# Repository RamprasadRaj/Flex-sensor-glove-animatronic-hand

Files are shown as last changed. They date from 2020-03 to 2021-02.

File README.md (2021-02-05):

# Flex sensor glove animatronic hand
Repository containing the information and files for flex sensor glove controlled 3 DoF animatronic hand
## Demo
This project deals with design, fabrication, and control of 3 finger 3 DoF animatronic hand mimicking flex sensor glove worn by human operator

[](https://youtu.be/1zQ_faMaoO8)

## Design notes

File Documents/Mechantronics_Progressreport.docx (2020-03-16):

MEGN540 - Project Progress Report

Ramprasad Rajagopalan

Bhuvan Tej Kanigiri

Technical:

What problem are you solving?

The project aims to design, fabricate and control 3 finger animatronic hand mirroring fingers movements made by a human operator. The project addresses a method to capture motion of fingers using flex sensors and fabricating a custom PCB to process, power and control the animatronic hand.

What is your design concept?

The hand design consists of three fingers viz., thumb, index and middle finger, with 1 DOF. Each finger has three portions viz., proximal, medial and distal portions. The different portions of the fingers are joint together with 1 or 2 springs and hinges on the dorsal side of the hand. 3D printing technique is utilised for printing each portion of the hand. Each finger is driven by a fishing line placed eccentrically on the palmer side of the hand. The finger movements are driven by the servo motors. One end of the fishing line is tied to the distal end of the finger and the other end is tied to the horn of the servo motor. The routing of the fishing line inside each finger is facilitated by having plastic straws enclosed within a hollow section. The entire setup is mounted on a platform having the custom PCB and power supply.

The glove design has flex sensors stitched to each finger for the entire length. The flex sensors are connected directly to the custom PCB by extending the wires. Later design may include wireless implementation.

What Sensors and Actuators will you use?

Here we are using flex sensors (datasheet (https://www.sparkfun.com/datasheets/Sensors/Flex/flex22.pdf)), which captures the bending movement data.

We are using an MG995 servo (datasheet (https://www.electronicoscaldas.com/datasheet/MG995_Tower-Pro.pdf)), which drives the animatronics hand.

What will your PCB do?

The custom PCB has the following components delivering certain processes.

- ATMega328P sits on a PCB board for all the required processing and communication purposes like converting flex sensor’s output voltage (digital output - ADC) to PWM timings (range: 0.388 - 2.14ms), in turn it calculates the duty cycle for the servo motor for the desired rotations, which finally replicates the human finger’s position.
- Potentiometer placed in the -ve terminal of the flex sensor would help in adjusting the sensitivity for the input users hand movement.
- Voltage regulator circuit to power the servo motors, sensors and ATMega328 separately.
- ICSP header to connect the external programmer to flash.
- Power jack to connect the external power supply.

All the heavy lifting is done in PCB and finally it sends the PWM commands to the servo motors.

What is your high-level integration plan?

Step 1: Human hand (uses a glove, where 3 flex sensors are attached to the 3 finger) gives finger movements, which are encoded in terms of resistance. Change of resistance in the three fingers implicitly knows how much it is moved - this is done using flex sensors. Take the analog output from the flex sensor, give it to ADC for conversion.

(https://www.google.com/aclk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)Step 2: Atmega328P receives this signal and converts that into a PWM signal using TIMERS.

Step 3: Finally power and PWM signal are sent to the servo motor on the animatronics hand.

Programmatic:

What is your project schedule and key milestones?

March 1st - 3rd week: Purchasing materials. 3D printing fingers and handbase. Building a breadboard prototype of the circuit. Pseudo code for reading the flex sensors data. Key milestone would be to have working finger movements in hand and programmable breadboard circuit.

March Fourth week(spring break): Fabricating the glove and writing the embedded C code for calibrating the flex sensor and controlling servo motor position. Implementing a filter to get a smooth response from the sensor. Key milestone would be to calibrate the flex sensor and implement the filter.

April 1st - 2nd week: Design and order the PCB. Testing for repeatability of finger actuation. Completing the left out work. Key milestone would be to have a functioning breadboard prototype of the animatronic hand.

April 3rd week: Further testing with custom PCB and Demo. Key milestone would be to have the PCB functioning with other components.

How have you split up the work?

Mechanical aspects of project: Ramprasad

Electronics aspects of project: Bhuvan Tej

Software aspects of project: both

What are your critical paths?

Arrival of sensors, motors and other components.

Getting the correct mapping of PWM values in the desired ranges.

Scaling is also critical - from the resistors value to the PWM signals.

Correct PCB design without shorting any components and arrival of functional PCB.

What is your current budget estimate?

Our current budget is around 100-120 USD ( ± 20 USD)

What is your highest technical risk and how are you mitigating that risk?

Hardware standpoint:

- As there all lots of electronics included on the PCB, make sure there is no shorting wire on PCB connections before giving supply: Using multimeter check all the connections properly for every iteration of testing it- if possible test in simulation software by giving some random test data within the specific range.
- The motor rotation should not exceed the finger movement limits: Start off with some small scaling component (High resistance for the resistor in series with sensor), then gradually increase it to the desired range.
- There is a chance of abduction/adduction finger movement happening instead of purely flexion/extension movement due to clearance in the joints or uneven force distribution along the finger. Having stoppers or adding 2 springs to each joint of the finger on the dorsal side makes sure that it's not moving sideways.

Software Standpoint:

- There is a chance sampling of some delay occurring from the user's hand movement to the animatronics hand, which can cause some loss of information in turn making the animatronics hand wobble randomly. Having a robust filter and sampling prevents the loss of information.

What is your highest programmatic risk and how are you mitigating that risk?

Higher chance of problem might be only from the hardware design standout point of view, design might change during the testing phase.

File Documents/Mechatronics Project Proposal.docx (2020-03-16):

Project Name: Animatronic Robotic Hand (Bhuvan Tej Kanigiri, Ramprasad Rajagopalan)

Concept proposal: From teleoperation to prosthetic hand development, animatronic hand serves as a “simple” implementation to mimic human hand movements. This project deals with design, fabrication and control of 3 finger 3 DOF animatronic “hand” mimicking flex sensor glove worn by human operator. The user wears the glove and the amount of bending in thumb, index and middle finger will be captured by the flex sensor attached on each finger. The amount of bending or resistance will be wirelessly transferred using custom build PCB to Arduino either over Wifi/bluetooth. The animatronic hand has fingers driven by strings and rubber band. The strings are attached to the servo motor. Based on the amount of bending, the Arduino will generate corresponding movement in the finger by driving the servo motors.

System requirements:

Servo Motors, Flex sensors (2.2”-4”), Arduino, 9v batteries, resistors, connecting pins, glove, thread, rubber band, foam board or cardboard, handbase, spacers and hobby knife.

Total Budget: USD $95 - (Electronic parts - $70, mechanical parts - $25)

Initial project plan:

February | - CAD design of 3 DOF 3 finger animatronics hand and base - Ordering sensor, motors and microcontroller - Working of Flex sensor, servo motors and setting wireless communication using breadboard circuit - Pseudo code and preliminary code for testing - Prototype 1 of hand and glove
March | - Refine CAD model - Design PCB and order - Embedded C code and testing - Prototype 2 of hand

April - Final testing and presentation

Design incorporation:

Interaction with the real world (minimum: one sensor & one affecter) - Flex sensor is attached to each finger on the glove worn by human operator. Servo motor is present to pull corresponding fingers. Embedded programming is used to program the Atmega328 microcontroller to read data from flex sensors and input PWM signals to control servo motor position. PCB design is done for incorporating power and wireless transmission from the glove. Final prototype should be able to mimic finger movement and demonstrate wireless transmission between glove and Arduino.

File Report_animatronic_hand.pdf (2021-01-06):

## Shadow hand - a 3 DoF animatronic hand

Ramprasad Rajagopalan
MS in Mechanical Engineering

rrajagopalan1@mines.edu

Bhuvan Tej Kanigiri
MS in Mechanical Engineering

bhuvantejkanigiri@mines.edu

Abstract

From teleoperation to prosthetic hand development, animatronic hand serves as a “simple” implementation to mimic human hand movements. This project deals with design, fabrication and control of 3 finger 3 DOF animatronic “hand” mimicking flex sensor glove worn by human operator. The user wears the glove and the amount of bending in thumb, index and middle finger is captured by the flex sensor attached on each finger. The amount of bending or resistance is sent to Arduino UNO for processing motor commands. The animatronic hand has fingers driven by strings and rubber band. Based on the amount of bending, the Arduino generates corresponding movement in the finger by driving the servo motors attached with the strings.

### 1. Introduction

### 1.1. Problem statement

Animatronic hand consists of two systems viz., mechatronic system of the hand and glove worn by the human operator. Only 3 degree of freedom(DoF) is considered out of the 27 DoF present in the human hand. These 3 DoF corresponds to flexion and extension of the middle, index and thumb fingers. The design problem is illustrated in Fig.1. The glove system consists of a design to capture the flexion and extension of each fingers. This can be done by using flex sensors or strain gauges attached to each finger. The flex sensors are placed on the dorsal side of the hand for easier design implementation. The bending data is sent directly to the micro-controller for processing motor commands. The mechatronic system consists of linkages making up the hand driven directly by the motors or by strings pulled by the motors. The linkages should be proportional to the human anatomical structure. The finger linkages are driven by fishing wire tied to each motor. The design should be done in a way to translate effective motion of the motors to maximum flexion movement of each fingers. The micro-controller should apply motor command values by mapping the input flex sensor data to corresponding angle. The re-

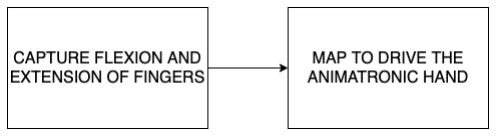
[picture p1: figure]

Figure 1. Design problem representation

quired components for building a 3 DoF animatronic hand driven by flex sensor glove is illustrated in the section below.

### 1.2. System Requirements

Electronics Components

Device name | Model no. | Quantity
Micro Servo Motors | A900 | 3
Flex sensors(2.2” - 4”) | - | 3
Arduino | UNO | 1
Programmer | AVRISP | 1
Resistors | 10K, 220 | 3,3
Jumper cables

Mechanical Components

Device name | Quantity
3D printed hand with hand base | 1
Glove | 1
Fishing thread and rubber band | 1
Insulation tape | 1

Software: Embedded C with Atmel Studio 6 and MAT-LAB for data visualization.

### 2. Approach

### 2.1. Design Implementation

The thumb, index and middle fingers of the right hand are chosen for mimicking the flexion and extension action. These three fingers are commonly used in robotic grippers for object manipulation and pick and place applications. Glove Design: The implemented glove design is shown in the left labelled image of Fig.3. The flex sensor is at-

Finger | Dimensions (mm)
Index Middle Thumb | 21 24 34 | 27 34 - | 48 56 28

Proximal
phalanx

Middle
phalanx

Distal
phalanx

Table 1. Dimension of each fingers

tached along the length on the dorsal side of the glove at roughly in the middle of the finger with tape. Other effective ways of fixing the flex sensor would be beneficial for better response and prevents unforced error in calibration. Animatronic hand design: The assembled CAD model and labelled 3D printed hand are shown in Fig.2 and 3 respectively. The 3D models are designed using Autodesk FUSION 360 software. The hand is designed according to human proportions and measurements as shown in Table.1. The bones in each finger is called as phalanx or phalange. The one closer to the metacarpals or torso of the hand is called as proximal phalanx and the one far from it is called as distal phalanx. The thumb finger is divided into 2 parts

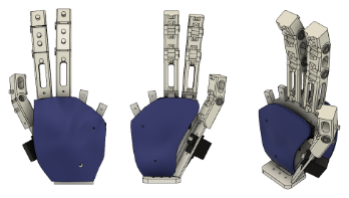
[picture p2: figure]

Figure 2. CAD assembly of animatronic hand

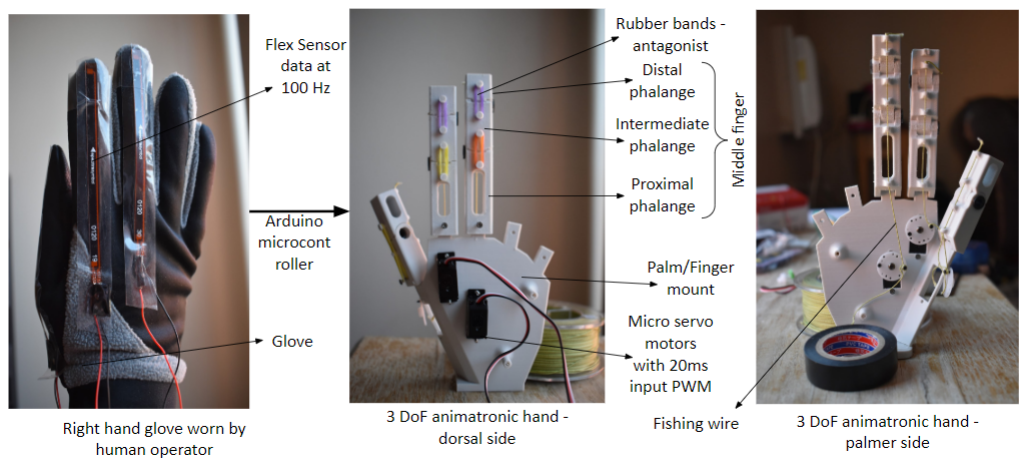
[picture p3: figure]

Figure 3. Labelled overview of solution

viz., proximal and distal phalanges while middle and index fingers are divided into 3 parts viz., proximal, intermediate and distal phalanges. The phalanges revolve relative to one another by revolute joint held with the help of plastic bush bearings. All the fingers are designed with the provision to route the fishing wire on the palmer side by providing extruding portions at end of each phalanx. The finger phalanges are also designed with extrusions at each ends on the dorsal side in order to tie the rubber band to the adjacent phalanges. The palm of the hand is designed in such a way that the thumb finger is fixed out-of-plane, to other fingers, in an opposing position as shown in Fig.2. The palm also has provision at the bottom to fix it onto the table.
One end of the fishing wire is tied to tip of the distal phalanx and other end is tied to the servo motor. The placement of the motors is pivotal in defining the range of motion and force exerted on the finger. The spindle of the servo is attached with round hub for compact design and larger force output. The mounting holes for servo motors are provided appropriately in order for it to be inserted in such a way that the spindle faces the palmer side of the hand. The hand design also consist of two form covers for aesthetic appeal and shielding the internal connections.

### 2.2. PCB Electronics

### 2.2.1 Circuit schematics

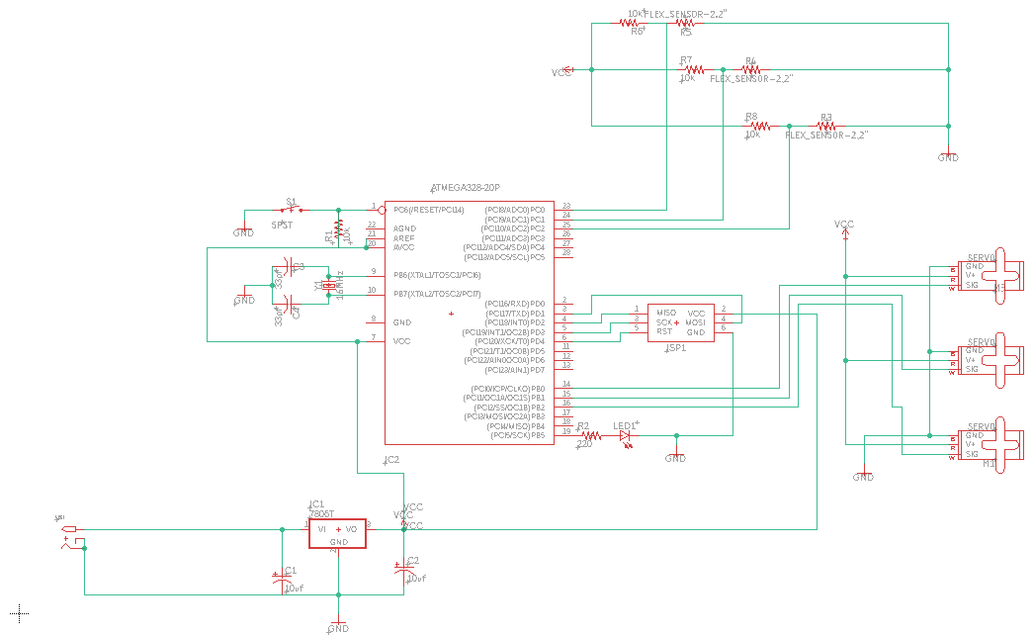
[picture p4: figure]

Figure 4. PCB schematics

Power Module: 12 V adaptor is connected to 7806T voltage regulator which serves to output constant voltage to the MCU section. This supply is given to three servos. MCU Module & Data transfer Module: Used Atmel Studio and AVR ISP programmer to compile the code in the PC and flash the program in the ATMega328P micro-controller.
Pin connections: From ISP to Atmega328P, it has six pins connected to MCU.
Electronics Components
C1: Table.2 is the connection from AVR-ISP programmer to Atmega328P micro controller.
C2: Table.3 is the connection from ATMega328P to flex sensors.
Note: Tapping is done in between the 10k resistor and Flex sensors, both sides are connected to ground and 5V

ISP pin | MCU
MOSI | PD1(TXD)- Pin 3
SPI | PD2(INT0)- Pin 4
Sck | PD3(INT1)- Pin 5
Reset | PD4(XCK/T0) - Pin 6
Vcc | Vin(Any 5v source)
Gnd | Gnd

Table 2. PIN connection between ISP and ATMega328P

MCU | Flex-sensor
PC0(ADC0) | Tapped in b/w Flex-I and 10k resistor(r6)
PC1(ADC1) | Tapped in b/w Flex-II and 10k resistor(r7)
PC2(ADC2) | Tapped in b/w Flex-III and 10k resistor(r8)

Table 3. PIN connections between flex sensor and ATMega328P

MCU | Micro servo motors
PB0 | Signal pin (named W) to servo1
PB1 | Signal pin (named W) to servo2
PB2 | Signal pin (named W) to servo3

Table 4. PIN connections between micro servo motor and AT-Mega328P

MCU | 16MHz Crystal oscillator
PB6(XTAL1) | crystal-oscillator one side
PB7(XTAL2) | crystal-oscillator other side

Table 5. PIN connection between crystal oscillator and AT-Mega328P

supply.
C3: Table.4 is the connection between ATMega328P and Micro-servo motors.
Note: The other two pins in each servo motor is connected to the supply. A 5V supply is provided but for an ideal working of servo motor, 6V is required. Due to lack of step-down converter equipment, suply is provided at 5V. As of now, there won’t be a considerable bias in servo motor characteristics, this is due to the proper threshold mapping done from the flex to servo accordingly by reducing the window.
C4: Table.5 is the connection between ATMega328P and 16MHz crystal oscillator.
I/O Device Module: Flex-sensor is used take input from the environment, where the user bends his hand (change of resistance: which will be the input signal for the EN pin in micro servo motor) and micro-servos act as a output device which bends the animatronics hand.

### 2.3. Programming

### 2.3.1 Motor control

The servo motors can be controlled using PWM signals of 20ms time period in order to make it rotate to the desired angle. The 16-bit TIMER1 of ATMega328P is utilised for generating the PWM signals with desired time period. Multiple PWM outputs can’t be achieved using TIMER1 OC1A pin. Therefore, the output voltage value of PORTB pins are controlled by TIMER1 to drive the servo motors. This can be achieved by comparing the TIMER1 count, TCNT1, value with the required motor voltage, motor vol, to clear the pin and compare match ISR to set the corresponding pin every 20ms. The value of motor vol is obtained from calibration. The clearing and setting of the pin generates the required PWM to control the motor.

### 2.3.2 Calibration

Flex sensor: The flex sensor data is read every 10ms and stored in a buffer. The data is initially streamed to MAT-LAB at 100Hz to record and visualize the signals. The streamed data is free from noise and thus eliminates the need for implementing a filter. The extremities of the data for each finger of a specific human operator are determined for flexion and extension. The values are then recorded for saturation and linear interpolation.
Servo motor: The servo motors has a limited range of motion i.e. from 0 deg to approx. 165 deg. The deadband of the servo motor is identified by setting different values to the motor vol in order to generate different duty cycle. These extremities are also recorded and used in linear interpolation and saturation. After identifying the deadband of servo motor, the round hub is appropriately placed at 0 deg with little tension in the fishing wire. This ensures that the motor pulls the finger right from the start of rotation.

### 2.3.3 Program flow chart

The extremities obtained from the calibration of the sensor and motor are included in the Embedded C program. The sequence of steps followed in programming the Embedded C program is shown in Fig.5. The initialization of the pin is done by setting PORTB pins as output. The TIMER1 is set in Fast-PWM mode with ICR1 as TOP and 8 as the prescalar value. The ICR1 value is chosen as 4999 in a way to generate PWM signals with 20ms time period. ISR for TIMER1 is called every 20ms to set PORTB pin value as HIGH in order to generate a non-inverting PWM signal. The TIMER0 is set in CTC mode with OCR0A as TOP. The value of OCR0A is set in a way to call an ISR on compare match every 10ms to raise flag 0 every 10ms, where flag 0 is defined as a volatile variable. The ADC is initialized with 1024 as prescalar without initialization the

ADMUX channel. By default, the MUX pins are set to read from pin A0.
A while loop is made to run infinitely by iterating through two different conditions. The first condition checks if the TCNT1 value is greater than the duty cycle value and PORTB pin value NOT set. If the condition gets passed then the PORTB pin value is set as LOW or cleared. The value of PORTB pin is set again when ISR of TIMER1 is called every 20ms. In order to reduce the load on the micro-controller to check this statement all time, an entry IF condition can be placed to check if the TCNT1 value lies within certain threshold of the ICR1 value. This helps in improving the performance of the micro-controller.
The second condition gets passed roughly every 10ms when flag 0 is raised. The current ADC value is read and stored. As it is not possible to read simultaneously from 3 analog pins, a SWITCH conditional clause is placed to map the analog value to corresponding motor voltage as well as switch the MUX pins. The ADC value is saturated within the calibration range before mapping. The MUX pin is set to read sequenctially between analog pins A0, A1, A2 and back again to A0. After the MUX pin value is set, another ADC conversion is started. The motor vol determines the duty cycle of the PWM signals.

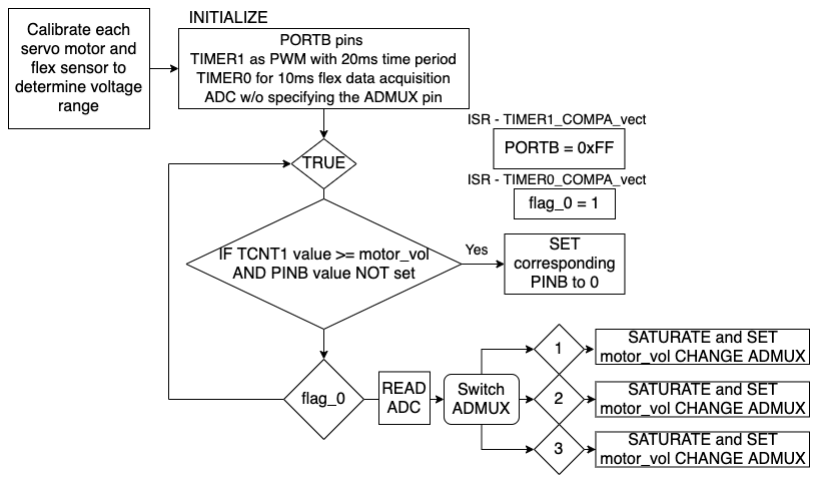
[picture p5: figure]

Figure 5. Pseudo code chart

### 3. Design challenges

The design process has certain critical and challenging steps that needs to be taken into consideration. The animatronic hand should be proportional to human anatomical structure. Unlike the human hand, animatronic hand is not driven by numerous independent linear actuating muscles but driven by single rotating motor. The effective force exerted by the motor depends immensely on the placement height and orientation. Effective pull length of approx. 28mm is delivered by the limited motion of the servo motor. The stiffness of the antagonist rubber band is critical and varies from joint to joint. The effective pull length and stiffness of the rubber band influences the bending angle of each finger. Fig.6 illustrates a finger joint in the actuated condition. The force exerted by the motor acts along the fishing wire. For a given pull length of the wire, the distance from the center of joint to the wire dictates the bending angle of each finger. If the distance increases the bending angle decreases and vice-versa. The effective torque from the motor should overcome the opposing torque of the rubber band. In addition, the opposing torque exerted by the rubber band should be sufficient enough to cause extension of the fingers.

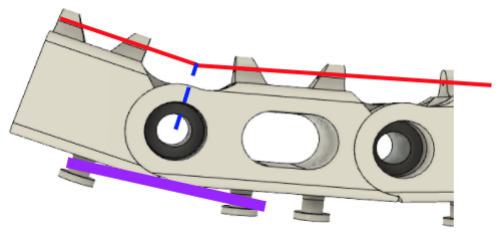
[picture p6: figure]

Figure 6. Side view of finger: Red line - fishing wire, Blue dashed line - distance from joint center and fishing wire and purple line -stretched rubber band

The servo motors with nylon gearing is sensitive to external loads. The gears and potentiometer can be easily damaged if the motor is manually turned. The flex sensor calibration can vary from person to person. Friction in the joints is undesirable and unavoidable in 3D printed parts. By overcoming the above mentioned challenges and considerations, a better design of the animatronic hand can be obtained.

### 4. Future Work and Lessons learnt

The 3 DoF animatronic hand is successfully controlled by tethered flex sensor glove. The next steps is to implement wireless data transfer in order to provide unconstrained interaction to the human operator. This promotes the scope for teleoperation applications. Better motors translate to better performance of the animatronic hand. Custom PCB with power distribution should be ordered and tested.
This project demonstrates the implementation of embedded programming and working with circular buffers. Some of the design challenges can be approached in a more systematic way. Kinematic study should be performed to optimize the geometry. An interactive approach to calibrate the sensor automatically before each run would be beneficial when used for multiple human operators.

### 5. References

[1] CoffeeCup Software, Inc. “The Animatronic Robotic Hand.” Animatronic Robotic Hand, URL. (https://mech.vub.ac.be/teaching/info/mechatronica/finished_projects_2013/team_5/index.html)
[2]“Learn the Fundamentals of Mechatronics!” Micro-controller - Program Transfer Part 1- A Beginners Guide to the Atmel AVR Atmega32, URL. (https://www.newbiehack.com/MicrocontrollerProgramTransferPart1ABeginnersGuidetotheAtmelAVRAtmega32.aspx)

### 6. Appendix

Video Demonstration link: Click here. (https://youtu.be/PWxeIW6LgmQ) Eagle CAD: attached
Embedded Code: attached

# PSEUDO CODE

## Demonstrating embedded programming for reading multiple flex sensor data and controlling multiple servo motors

## PROGRAM: Reading analog values from flex sensors and controlling the servo motors

DESCRIPTION: Flexion and extension of a finger is captured by change in voltage across the flex sensors. The analog voltage is read and mapped to corresponding control voltage for each servo motors. The PWM signal is controlled with TIMER1 at 50Hz and data acquisition is done with TIMER0 at 100Hz.

## FUNCTION: pin_init INPUT: None RETURNS: None

## INITIALIZE data direction register of PORTB, DDRB as OUTPUT

## FUNCTION: timer_init INPUT: None RETURNS: None

## INITIALIZE TCNT1 and TCNT0 as 0, SET TIMER1 in fastPWM mode with ICR1 as 4999 as TOP and

8 as prescaler value to generate non-inverting PWM signals at 50Hz, SET TIMER0 in CTC mode with OCR0A as 156 as TOP and 1024 as prescaler value to raise flag every 10ms and enable interrupts for both timers.

## FUNCTION: ISR INPUT: TIMER1_COMPA_vect RETURNS: None

## SET PORTB as 0xFF (HIGH)

## FUNCTION: ISR INPUT: TIMER0_COMPA_vect RETURNS: None

## flag_0 as 1

## FUNCTION: adc_init INPUT: None RETURNS: None

## INITIALIZE ADMUX and SET REFS0, ENABLE ADC in ADCSRA register with 128 as prescaler value using ADPSx pins

## FUNCTION: adc_read INPUT: None RETURNS: ADC

## RETURN ADC

## FUNCTION: uart_init INPUT: None RETURNS: None

INITIALIZE the baudrate registers UBRR0 and transmission and receiver pins in UCSR0B and SET

## the data bits to be 8-bit long in UCSR0C register

## FUNCTION: uart_transmit INPUT: data RETURNS: None

## UDR0 as data

## FUNCTION: sensor_middle_to_motor INPUT: sense_pos RETURNS: motor_vol

## CALCULATE mapping using linear interpolation to convert sense_pos to motor_vol

## FUNCTION: sensor_index_to_motor INPUT: sense_pos RETURNS: motor_vol

## CALCULATE mapping using linear interpolation to convert sense_pos to motor_vol

## FUNCTION: sensor_thumb_to_motor INPUT: sense_pos RETURNS: motor_vol

## CALCULATE mapping using linear interpolation to convert sense_pos to motor_vol

## FUNCTION: main INPUT: None RETURNS: None

INITIALIZE flexthumb, flexmiddle, flexindex variables, pin_init, uart_init, timer_init, adc_init,

## float buffer to store the flex sensor data and start an ADC conversion

## FOR ALL TIME IF TCNT1>100 AND TCNT1<800 // removing overload on micro-controller IF TCNT1 >= middle_count AND bit_is_set(PORTB, PINB1) PORTB &= ~(1<<PINB1)

## IF TCNT1 >= index_count AND bit_is_set(PORTB, PINB2) PORTB &= ~(1<<PINB2)

## IF flag_0 IF !(ADCSRA & (1<<ADSC)) // ADC conversion is done SET adcValue as adc_read()

## SWITCH ADMUX CASE 0x40 SET flexValue as adcValue SATURATE flexValue within calibration limit SET middle_count as sensor_middle_to_motor(flexValue) SET ADMUX as 0x41

## CASE 0x41 SET flexValue as adcValue SATURATE flexValue within calibration limit SET middle_count as sensor_index_to_motor(flexValue) SET ADMUX as 0x42

## CASE 0x42 SET flexValue as adcValue SATURATE flexValue within calibration limit SET middle_count as sensor_thumb_to_motor(flexValue) SET ADMUX as 0x40

## Start another ADC conversion SET flag_0 as 0 // reset for TIMER0

## RETURN 0

/*
* animatronics.c
*
* Created: 4/24/2020 11:34:49 PM
* Author: Ramprasad Rajagopalan and Bhuvan Tej Kanigiri */

#ifndef F_CPU

#define F_CPU 16000000UL

#endif

#include <stdio.h>

#include <avr/io.h>

#include <avr/interrupt.h>

#include "Ring_Buffer.h"

#define BAUD 9600

#define BAUDRATE ((F_CPU/(BAUD*16UL))-1)

// Flag to raise for sending data to MATLAB volatile uint8_t flag_0 = 0;

//initialization
void pin_init(void)
{
//A0 is connected to flex sensor 1 //A1 is connected to flex sensor 2 //A3 is connected to flex sensor 3 DDRB = 0xFF;
//PB1 is connected to servo1 //PB2 is connected to servo2 //PB3 is connected to servo3 }

void timer_init(void){
// Set initial timer value
TCNT0 = 0; // Serial communication
TCNT1 = 0; //
// CTC mode with prescaler as 8 for TIMER1
TCCR1A |= (1<<WGM11);
TCCR1B |= (1<<WGM13)|(1<<WGM12)|(1<<CS11)|(1<<CS10); // Set ICR1A as top value for 10ms duty cycle
ICR1 = 4999;
// CTC mode with prescaler as 1024 for TIMER0 TCCR0B = (1<<WGM02)|(1<<CS02)|(1<<CS00);
// Compare value for 10ms sampling rate OCR0A = 156;
// Enable compare interrupt
TIMSK1 |= (1<<OCIE1A);
TIMSK0 = (1<<OCIE0A);
}

ISR(TIMER1_COMPA_vect){
PORTB = 0xFF;
}

ISR(TIMER0_COMPA_vect){
flag_0 = 1;

}

// Initialize ADC
void adc_init(void)
{
// Set V_ref and set to read from pin ADC1
ADMUX = (1<<REFS0);
// Set prescaler to 128 and Enable ADC
ADCSRA = (1<<ADPS2)|(1<<ADPS1)|(1<<ADPS0)|(1<<ADEN); }

// Read and return ADC value
uint16_t adc_read()
{
// Return the ADC value
return(ADC);
}

void uart_init(void)
{
// Initialize baudrate registers
UBRR0H = (BAUDRATE>>8);
UBRR0L = BAUDRATE;
// Initialize transmission and receiver pins UCSR0B = (1<<TXEN0)|(1<<RXEN0);
// Set data bits to be 8-bits long
UCSR0C = (0<<USBS0)|(1<<UCSZ00)|(1<<UCSZ01); }

// Transmit data serially
void uart_transmit(unsigned char data)
{
// Load to UART buffer
UDR0 = data;
}

// Function to interpolate middle finger position int sensor_middle_to_motor(int sense_pos)
{
int motor_pos;
motor_pos = (-4.7*sense_pos) + 2494; return motor_pos;
}

// Function to interpolate index finger position int sensor_index_to_motor(int sense_pos)
{
int motor_pos;
motor_pos = (-4.3*sense_pos) + 2822.4; return motor_pos;
}

int main(void){
// Variable for flexThumb
int flexthumb = 0;
// variable for flexmiddle int flexmiddle = 0;
// variable for flexindex

int flexindex = 0;
// variable to control PWM input for middle finger and index finger int middle_count, index_count;
// Clear all interrupts
cli();
// Initialize the pins
pin_init();
// Initialize serial communication pins uart_init();
// Initialize timer pins and interrupts timer_init();
// Initialize PWM
pwm_init();
// Initialize ADC
adc_init();
// Initialize global interrupts
sei();
// Start conversion and wait for it to be done ADCSRA |= (1<<ADSC);
// Filter initialization
struct Ring_Buffer_F buffer_thumb; rb_initialize_F(&buffer_thumb); struct Ring_Buffer_F buffer_pointing; rb_initialize_F(&buffer_pointing); struct Ring_Buffer_F buffer_middle; rb_initialize_F(&buffer_middle);
// Initialize output char buffer struct Ring_Buffer_C p_buf; rb_initialize_C(&p_buf);
//main loop
while (1)
{
if (TCNT1>100 && TCNT1<800)
{
if (TCNT1>=middle_count && bit_is_set(PORTB,PINB1)) {
PORTB &= ~(1<<PINB1);
}
if (TCNT1>=index_count && bit_is_set(PORTB,PINB2)) {
PORTB &= ~(1<<PINB2);
}
}

if (flag_0)
{
// Check if ADC conversion is done if (!(ADCSRA & (1<<ADSC)))
{
uint16_t adcValue = adc_read(); // switch the pin
switch (ADMUX)
{
case 0x40:
flexmiddle = adcValue;
if (flexmiddle<405) flexmiddle = 405; else if (flexmiddle>500) flexmiddle = 500;

middle_count =
sensor_middle_to_motor(flexmiddle); ADMUX = 0x41;
break;
case 0x41:
flexindex = adcValue;
if (flexindex<505) flexindex = 505;
else if (flexindex>620) flexindex = 620; index_count = sensor_index_to_motor(flexindex); ADMUX = 0x42;
break;
case 0x42:
flexthumb = adcValue;
ADMUX = 0x40;
break;
}
// start the next conversion
ADCSRA |= (1<<ADSC);

/*uint8_t *numByte = (uint8_t *) &flexindex; rb_push_back_C(&p_buf, numByte[0]); rb_push_back_C(&p_buf, numByte[1]); rb_push_back_C(&p_buf, numByte[2]); rb_push_back_C(&p_buf, numByte[3]);*/ }
// Reset flag for timer0
flag_0 = 0;
}

/*// Check if output buffer has byte and UART serial is free if ((rb_length_C(&p_buf)!=0) && (UCSR0A & (1<<UDRE0)))
{
// Load to UART buffer
uart_transmit(rb_pop_front_C(&p_buf));
}*/
}
return 0;
}

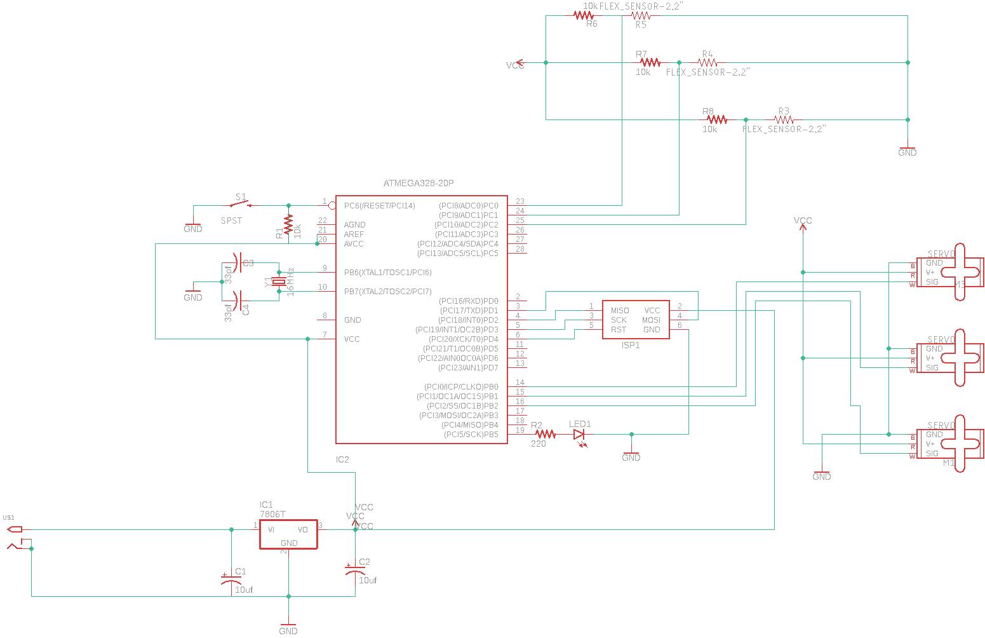
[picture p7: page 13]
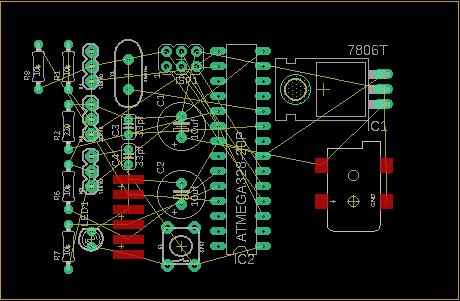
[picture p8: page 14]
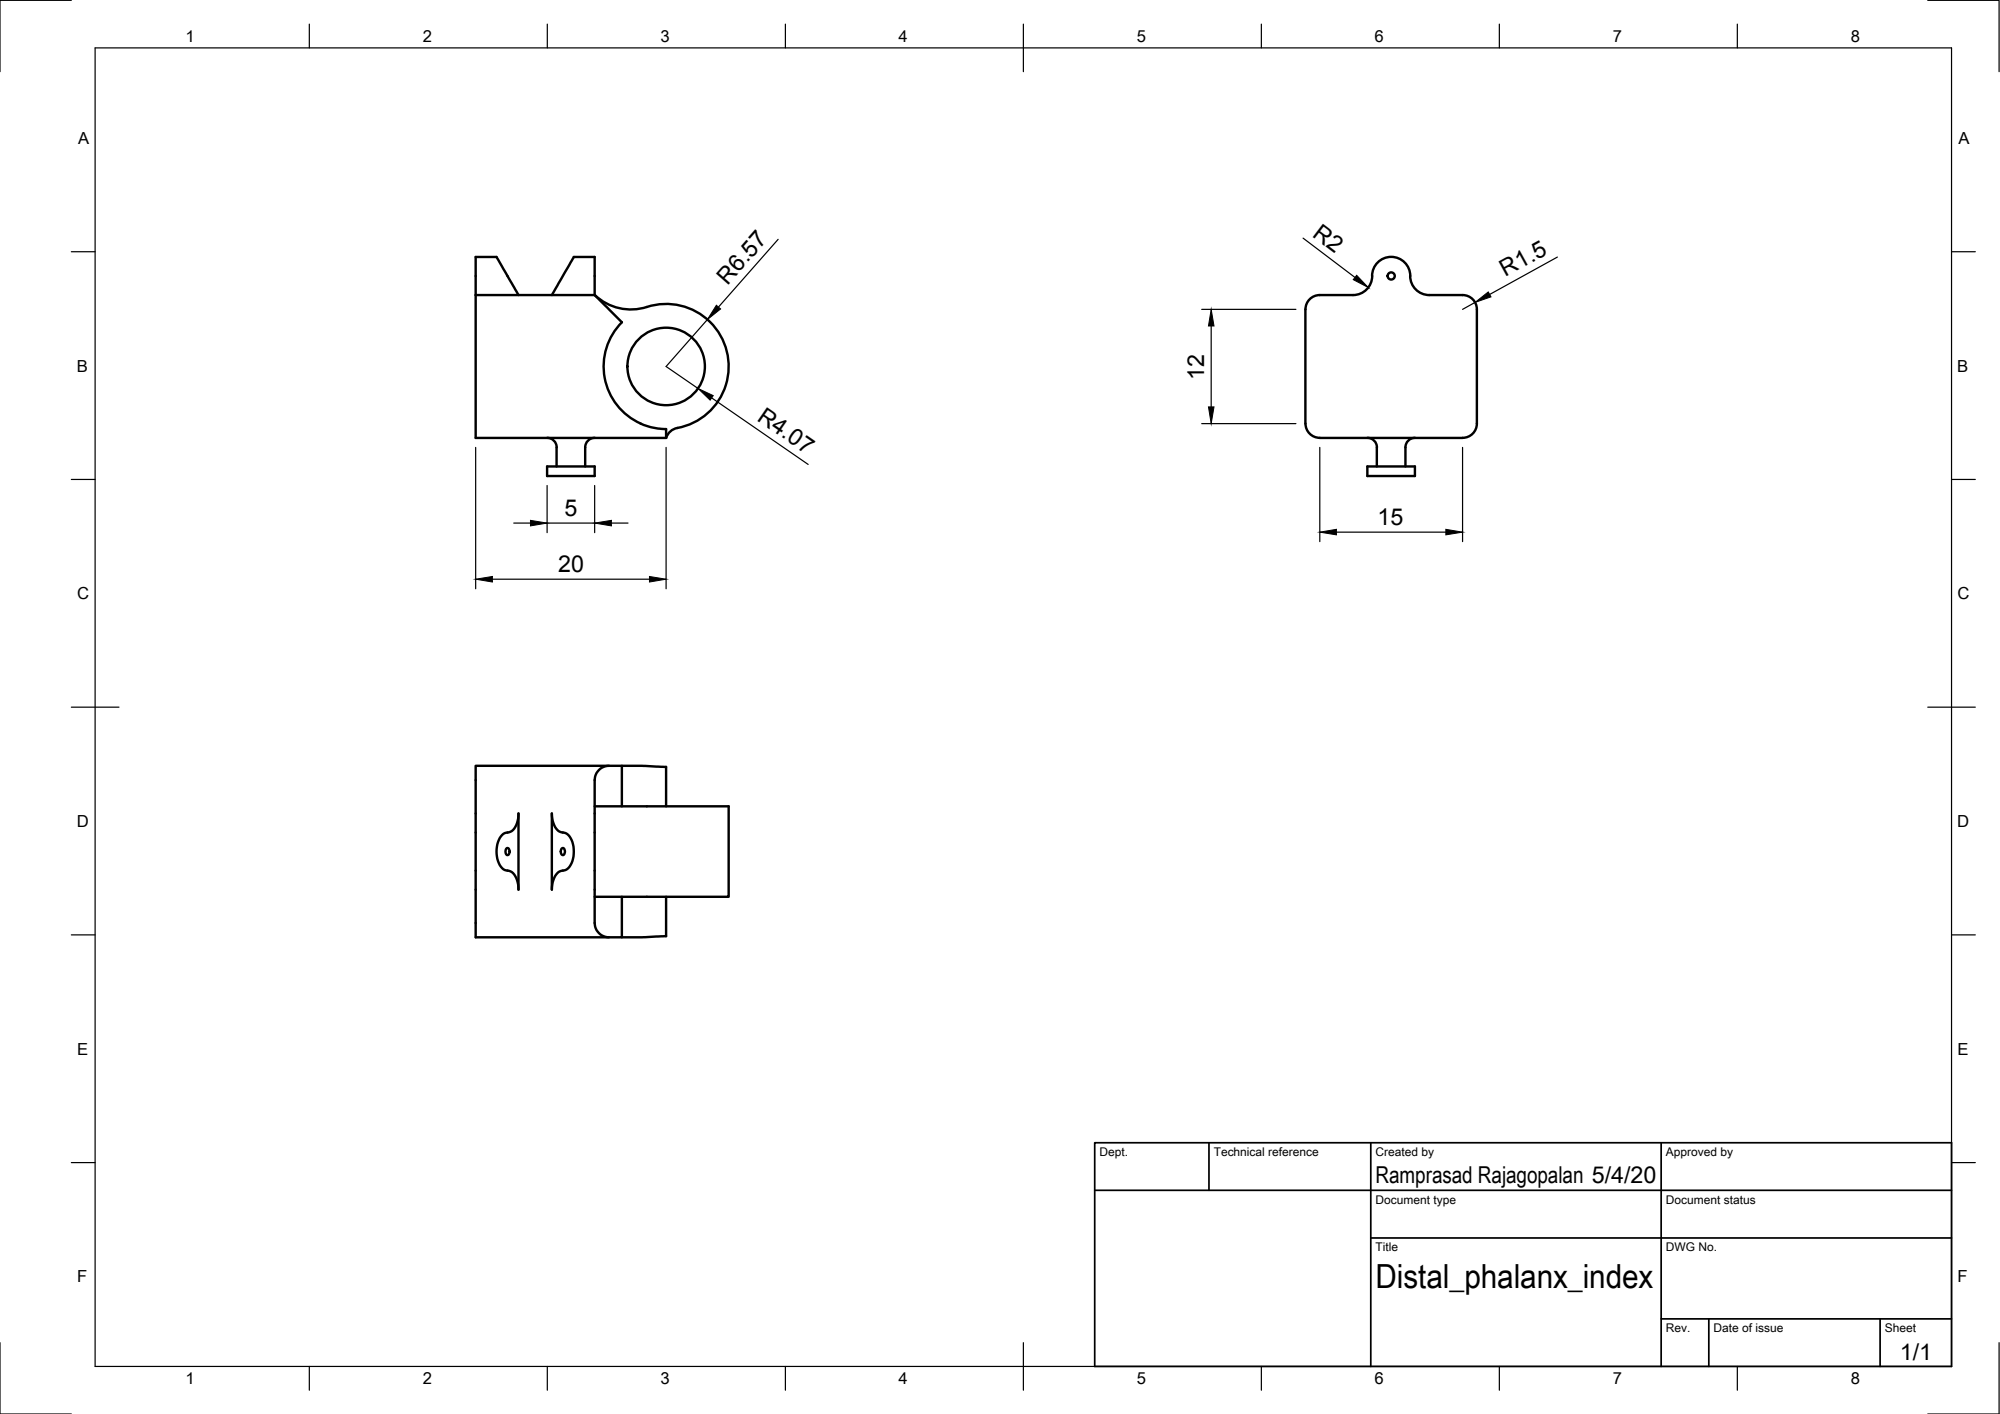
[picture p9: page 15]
Dept.; Technical reference; Created by; Approved by; Document type; Document status

Ramprasad Rajagopalan ¹²

Title Distal_phalanx_index | DWG No.

Rev. | Date of issue | Sheet

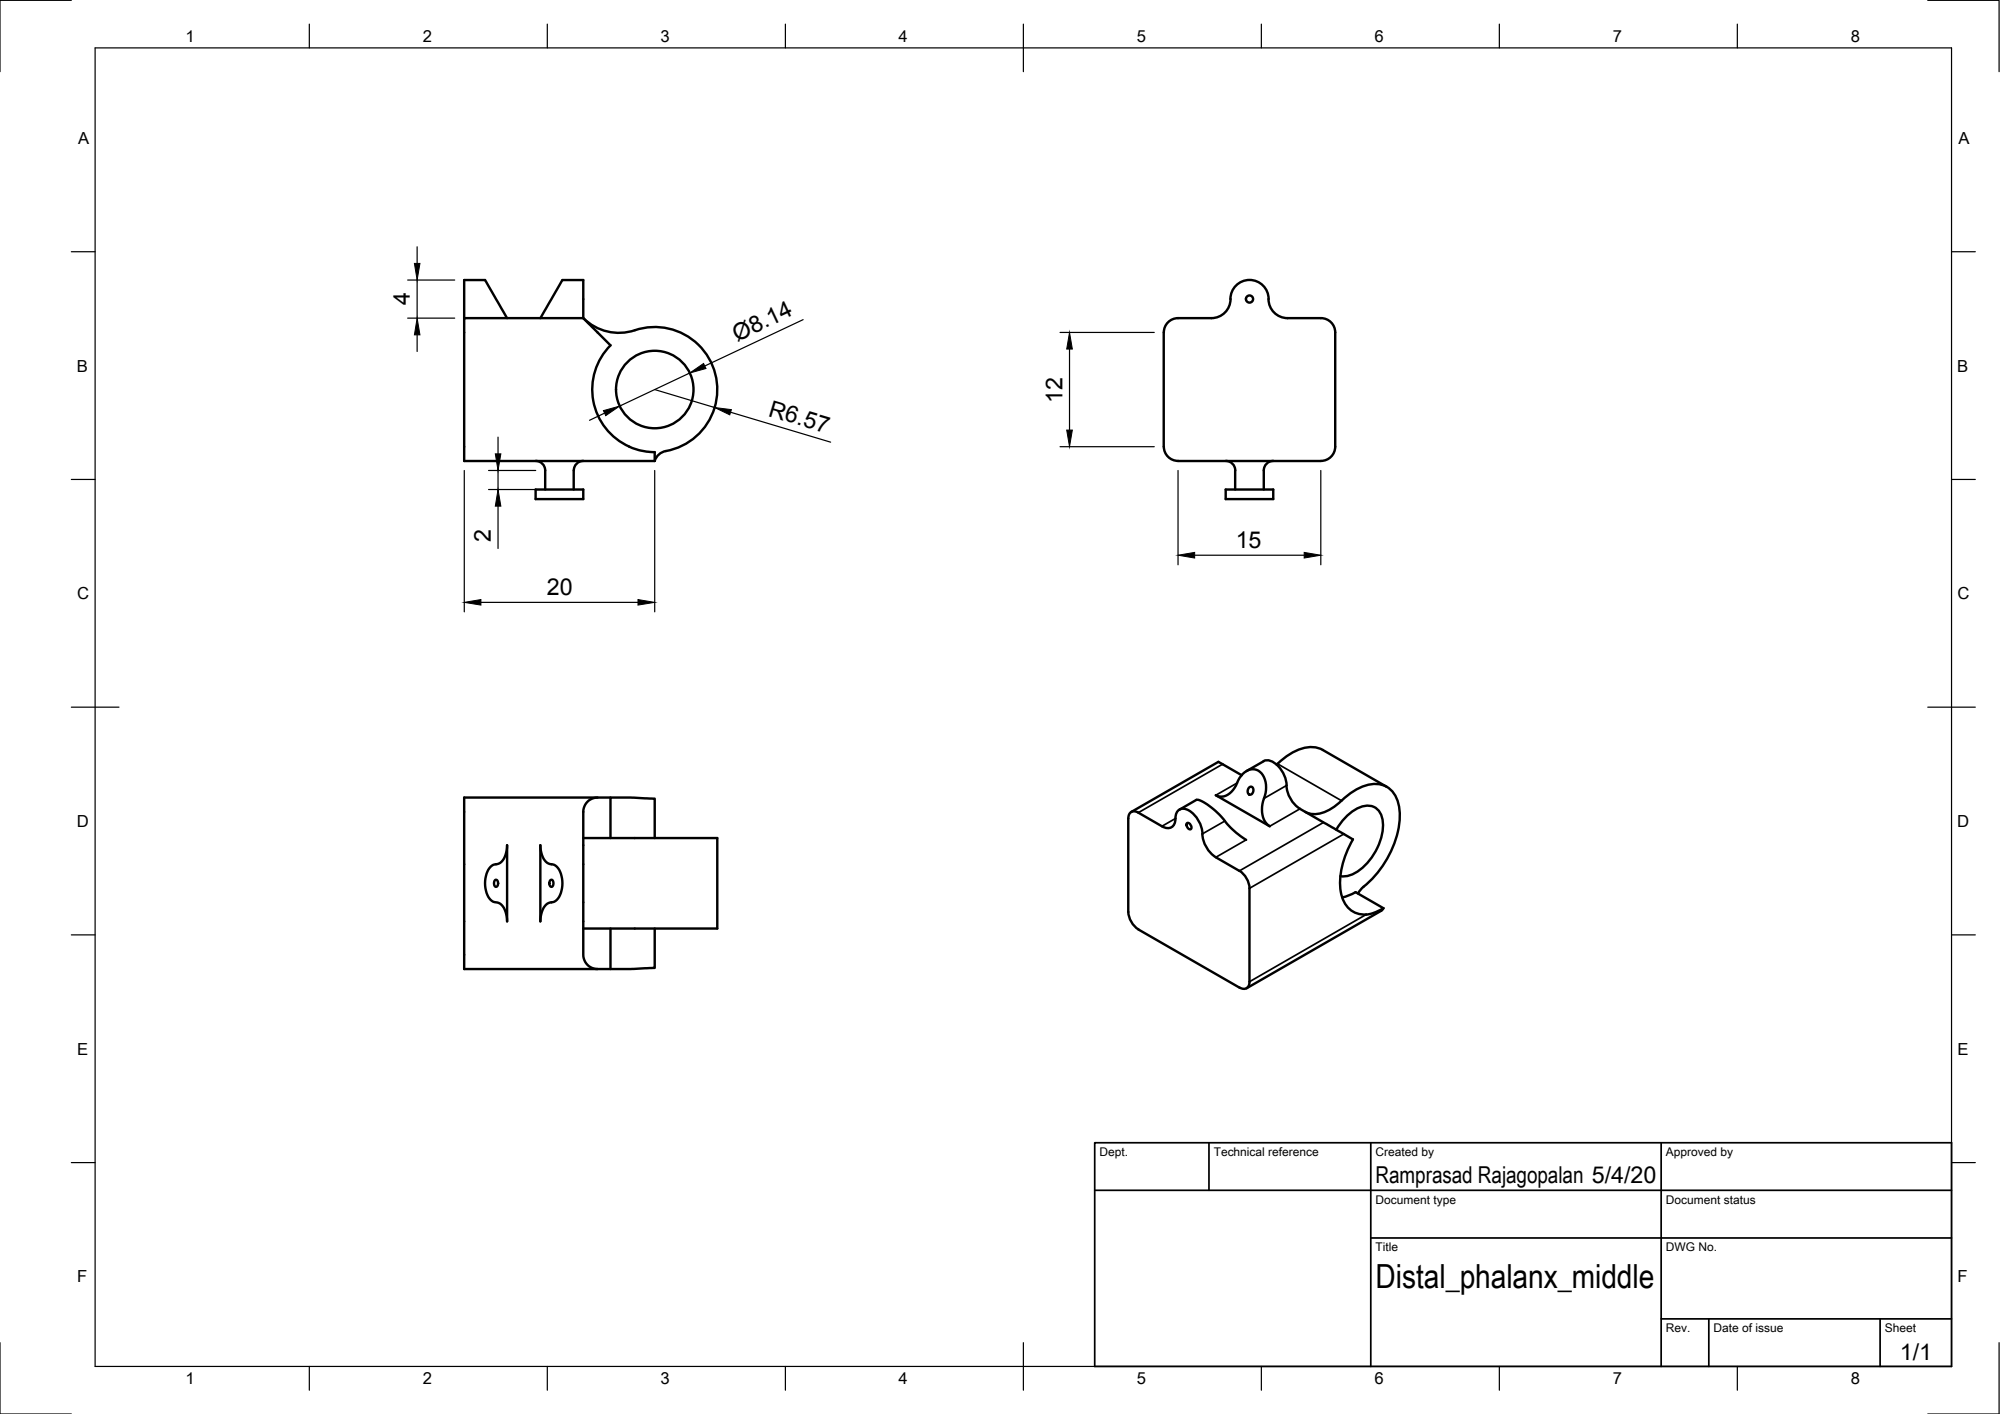
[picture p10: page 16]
Dept.; Technical reference; Created by; Approved by; Document type; Document status; Title; DWG No.; Distal_phalanx_middle; Ramprasad Rajagopalan

2.19 | 12

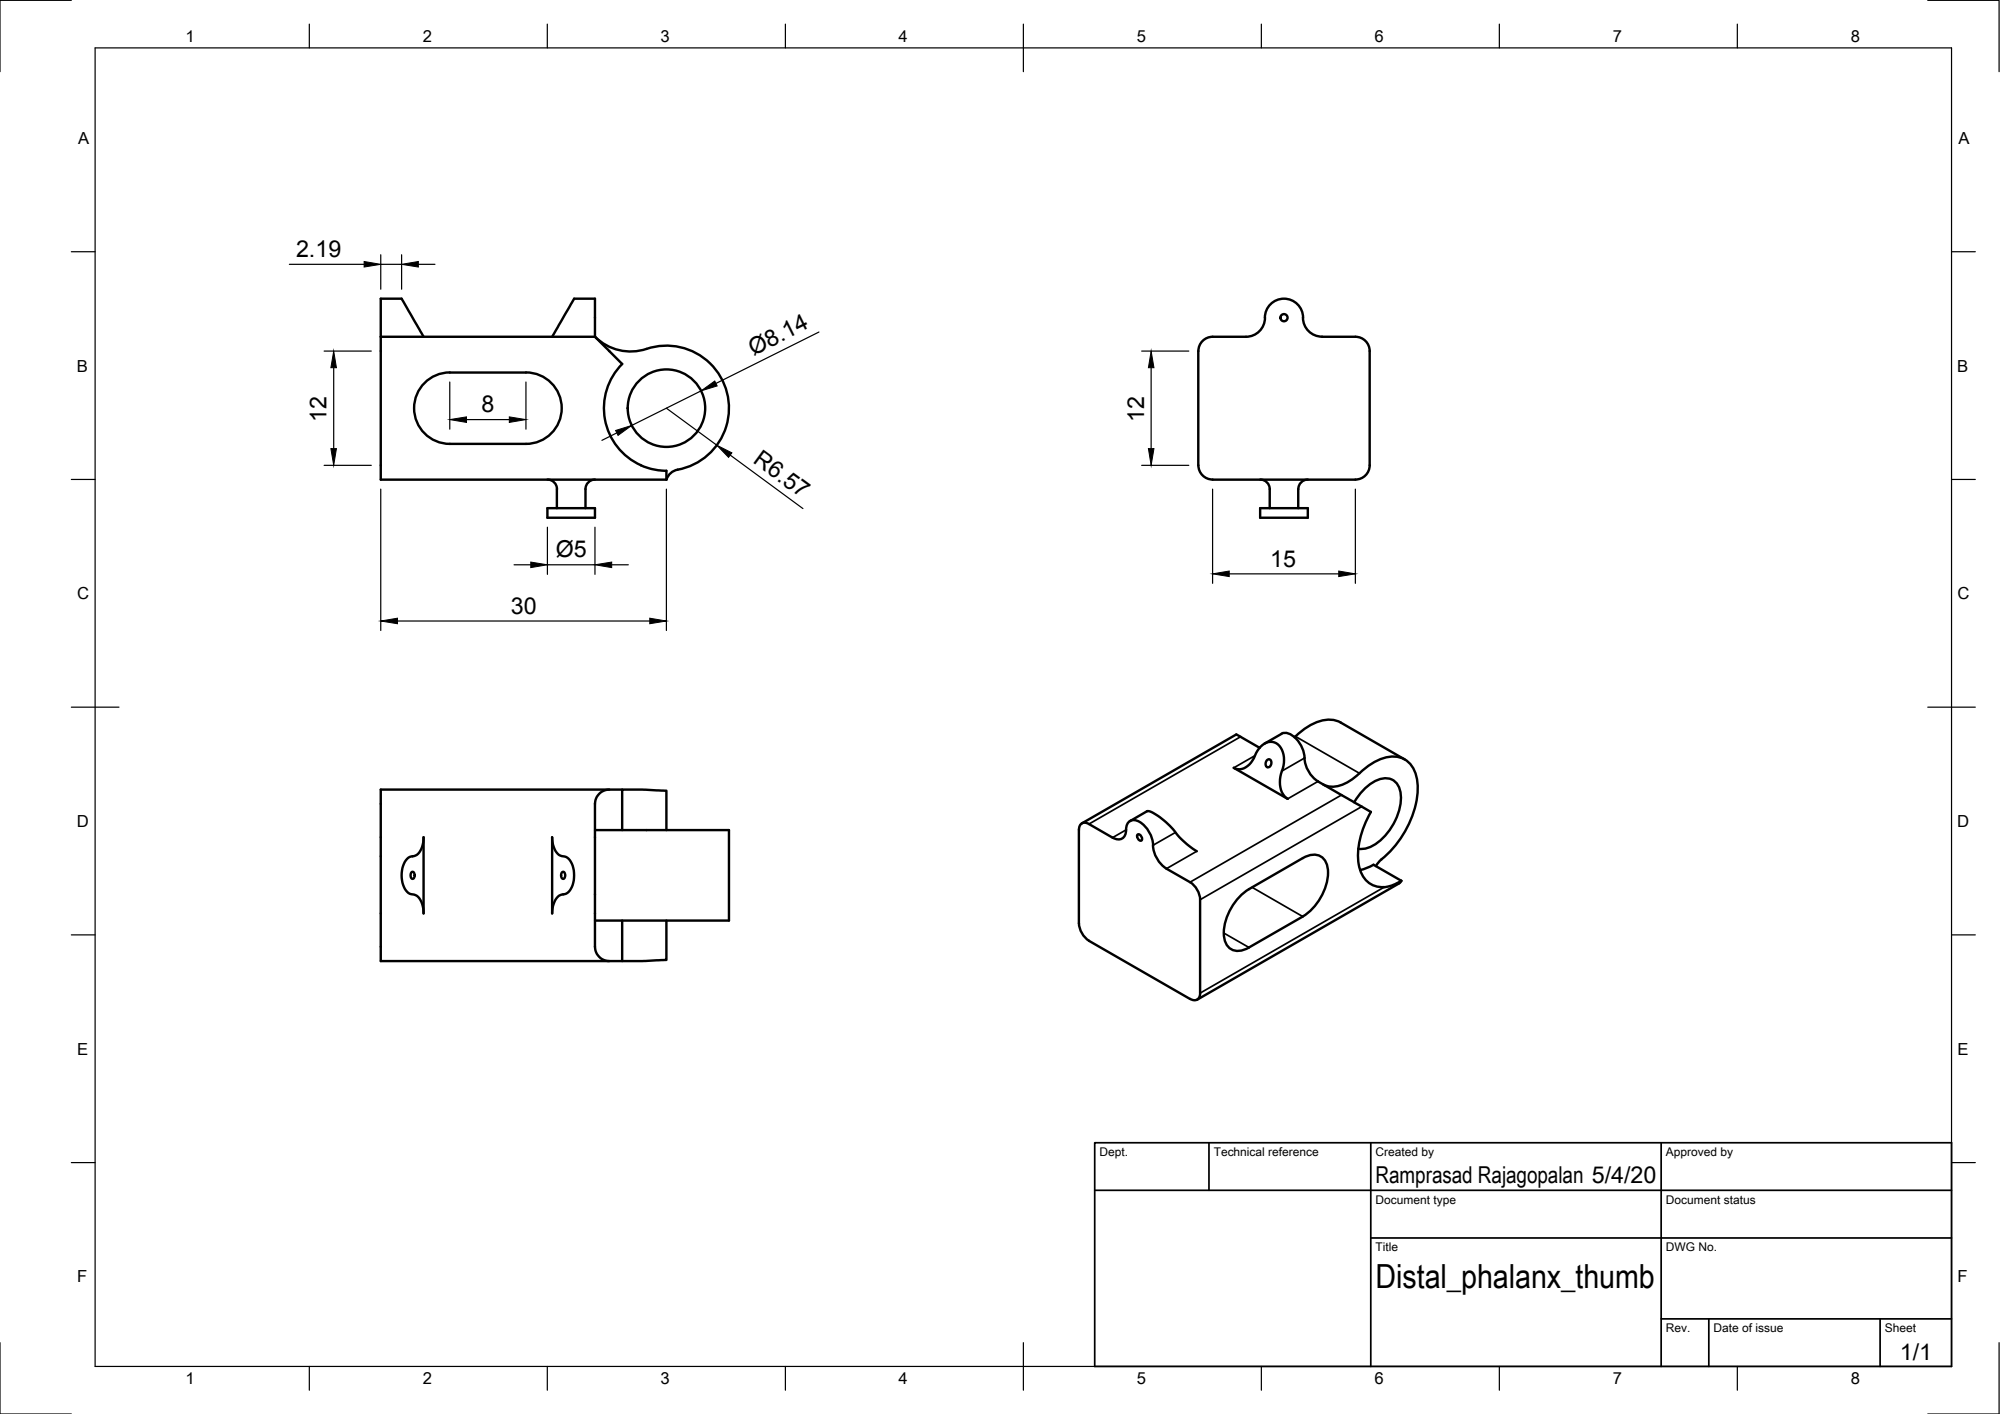
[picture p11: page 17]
Dept.; Technical reference; Created by; Approved by; Document type; Document status; Title; DWG No.; Distal_phalanx_thumb

Ramprasad Rajagopalan ¹²

15

3

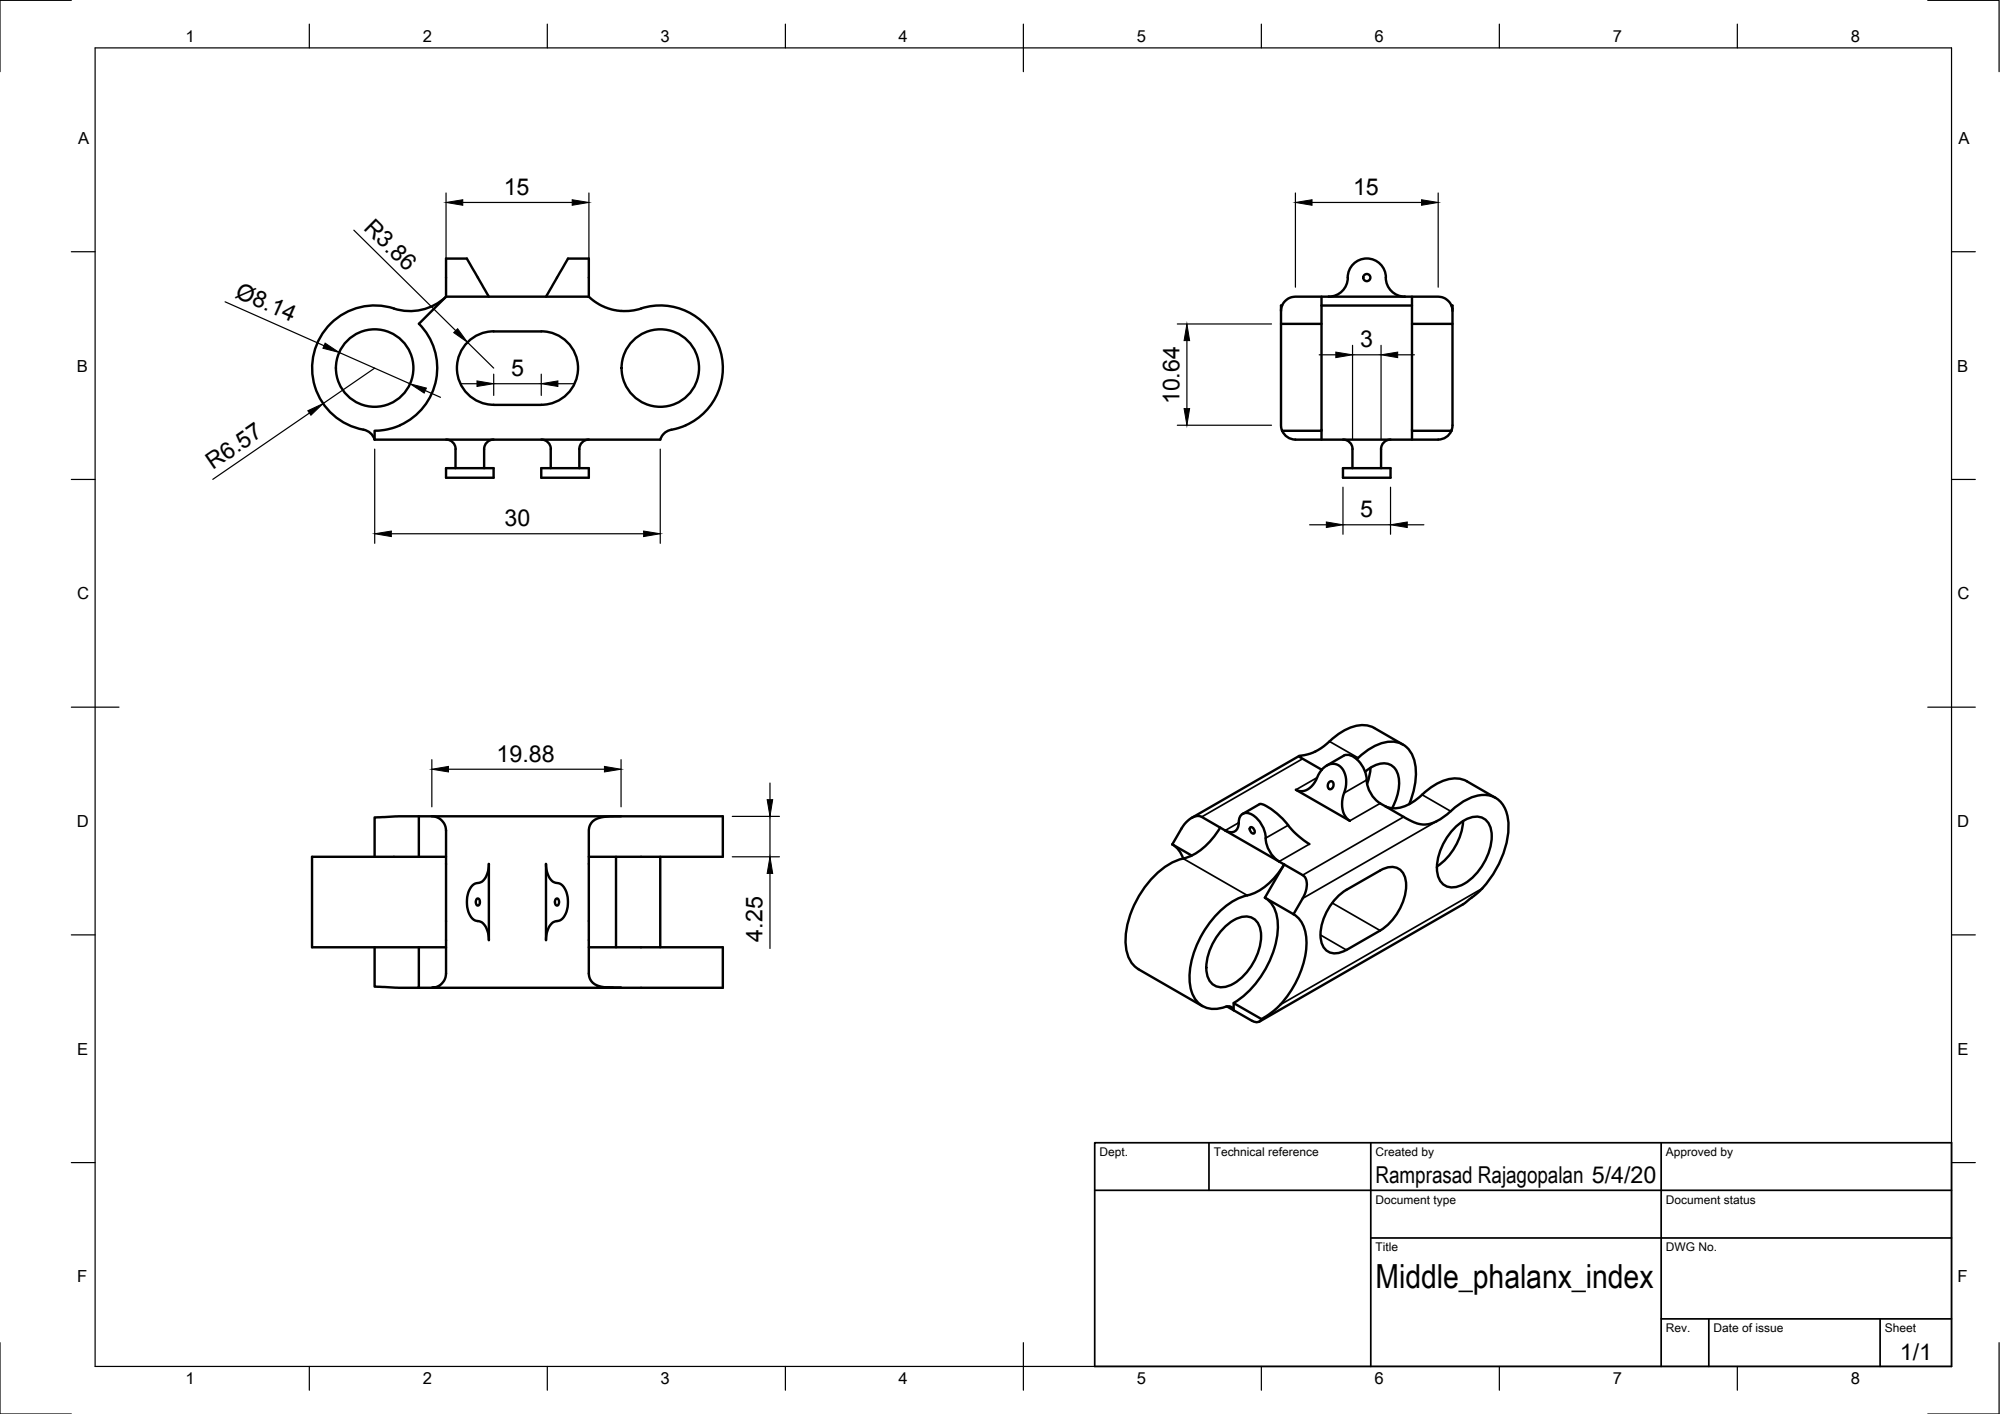
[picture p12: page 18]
Dept.; Technical reference; Created by; Approved by; Document type; Document status; Title; DWG No.; Middle_phalanx_index; Ramprasad Rajagopalan

17

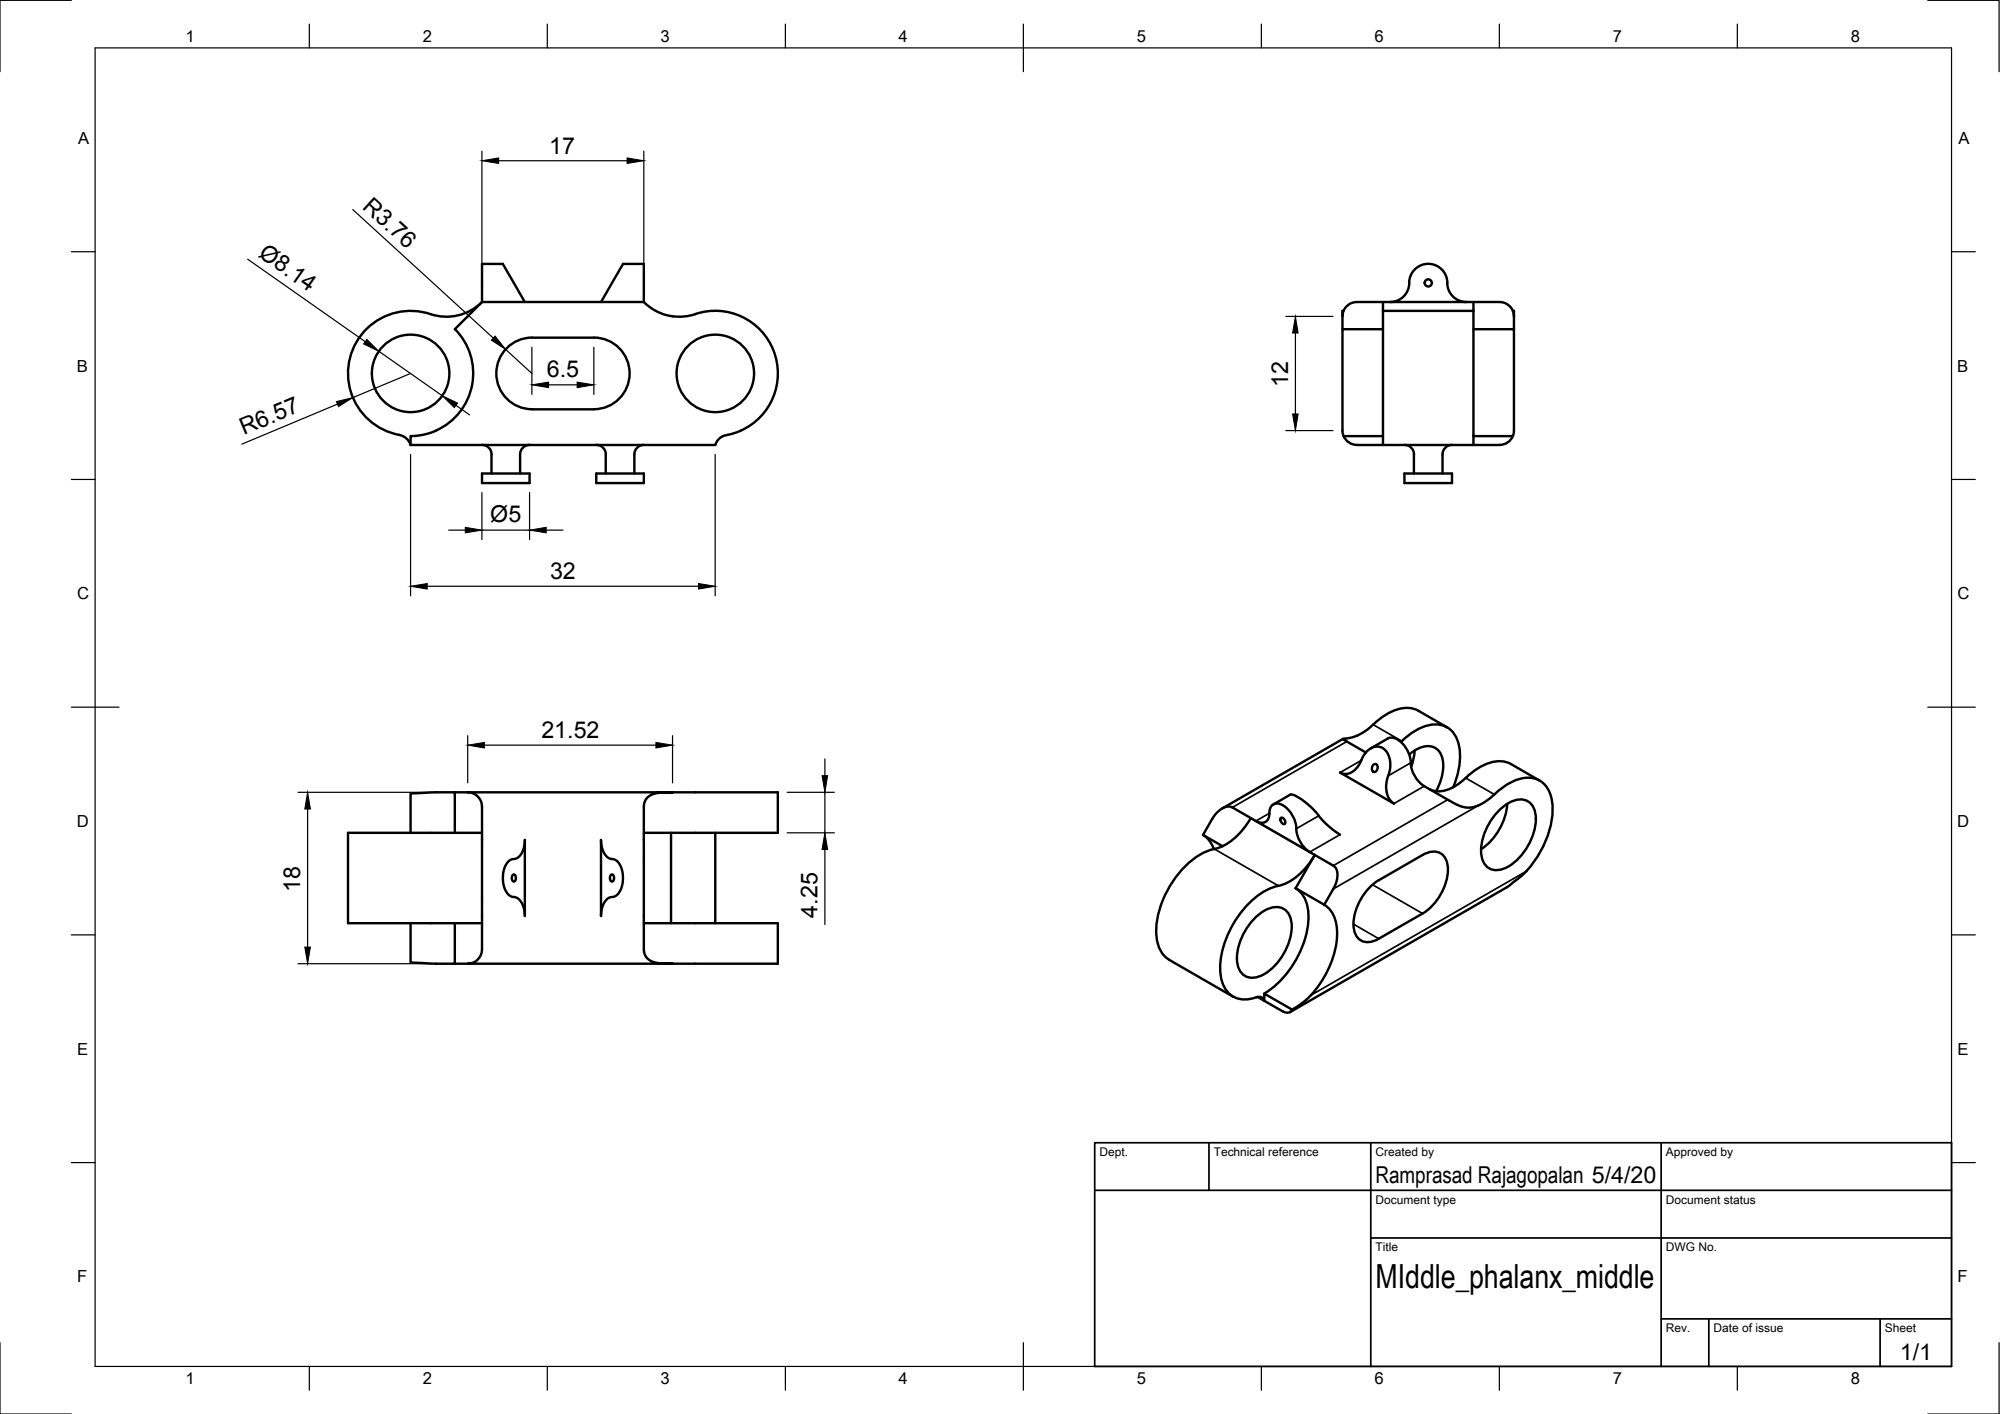
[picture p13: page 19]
Dept.; Technical reference; Created by; Approved by; Document type; Document status; Title; DWG No.; MIddle_phalanx_middle; Ramprasad Rajagopalan

32

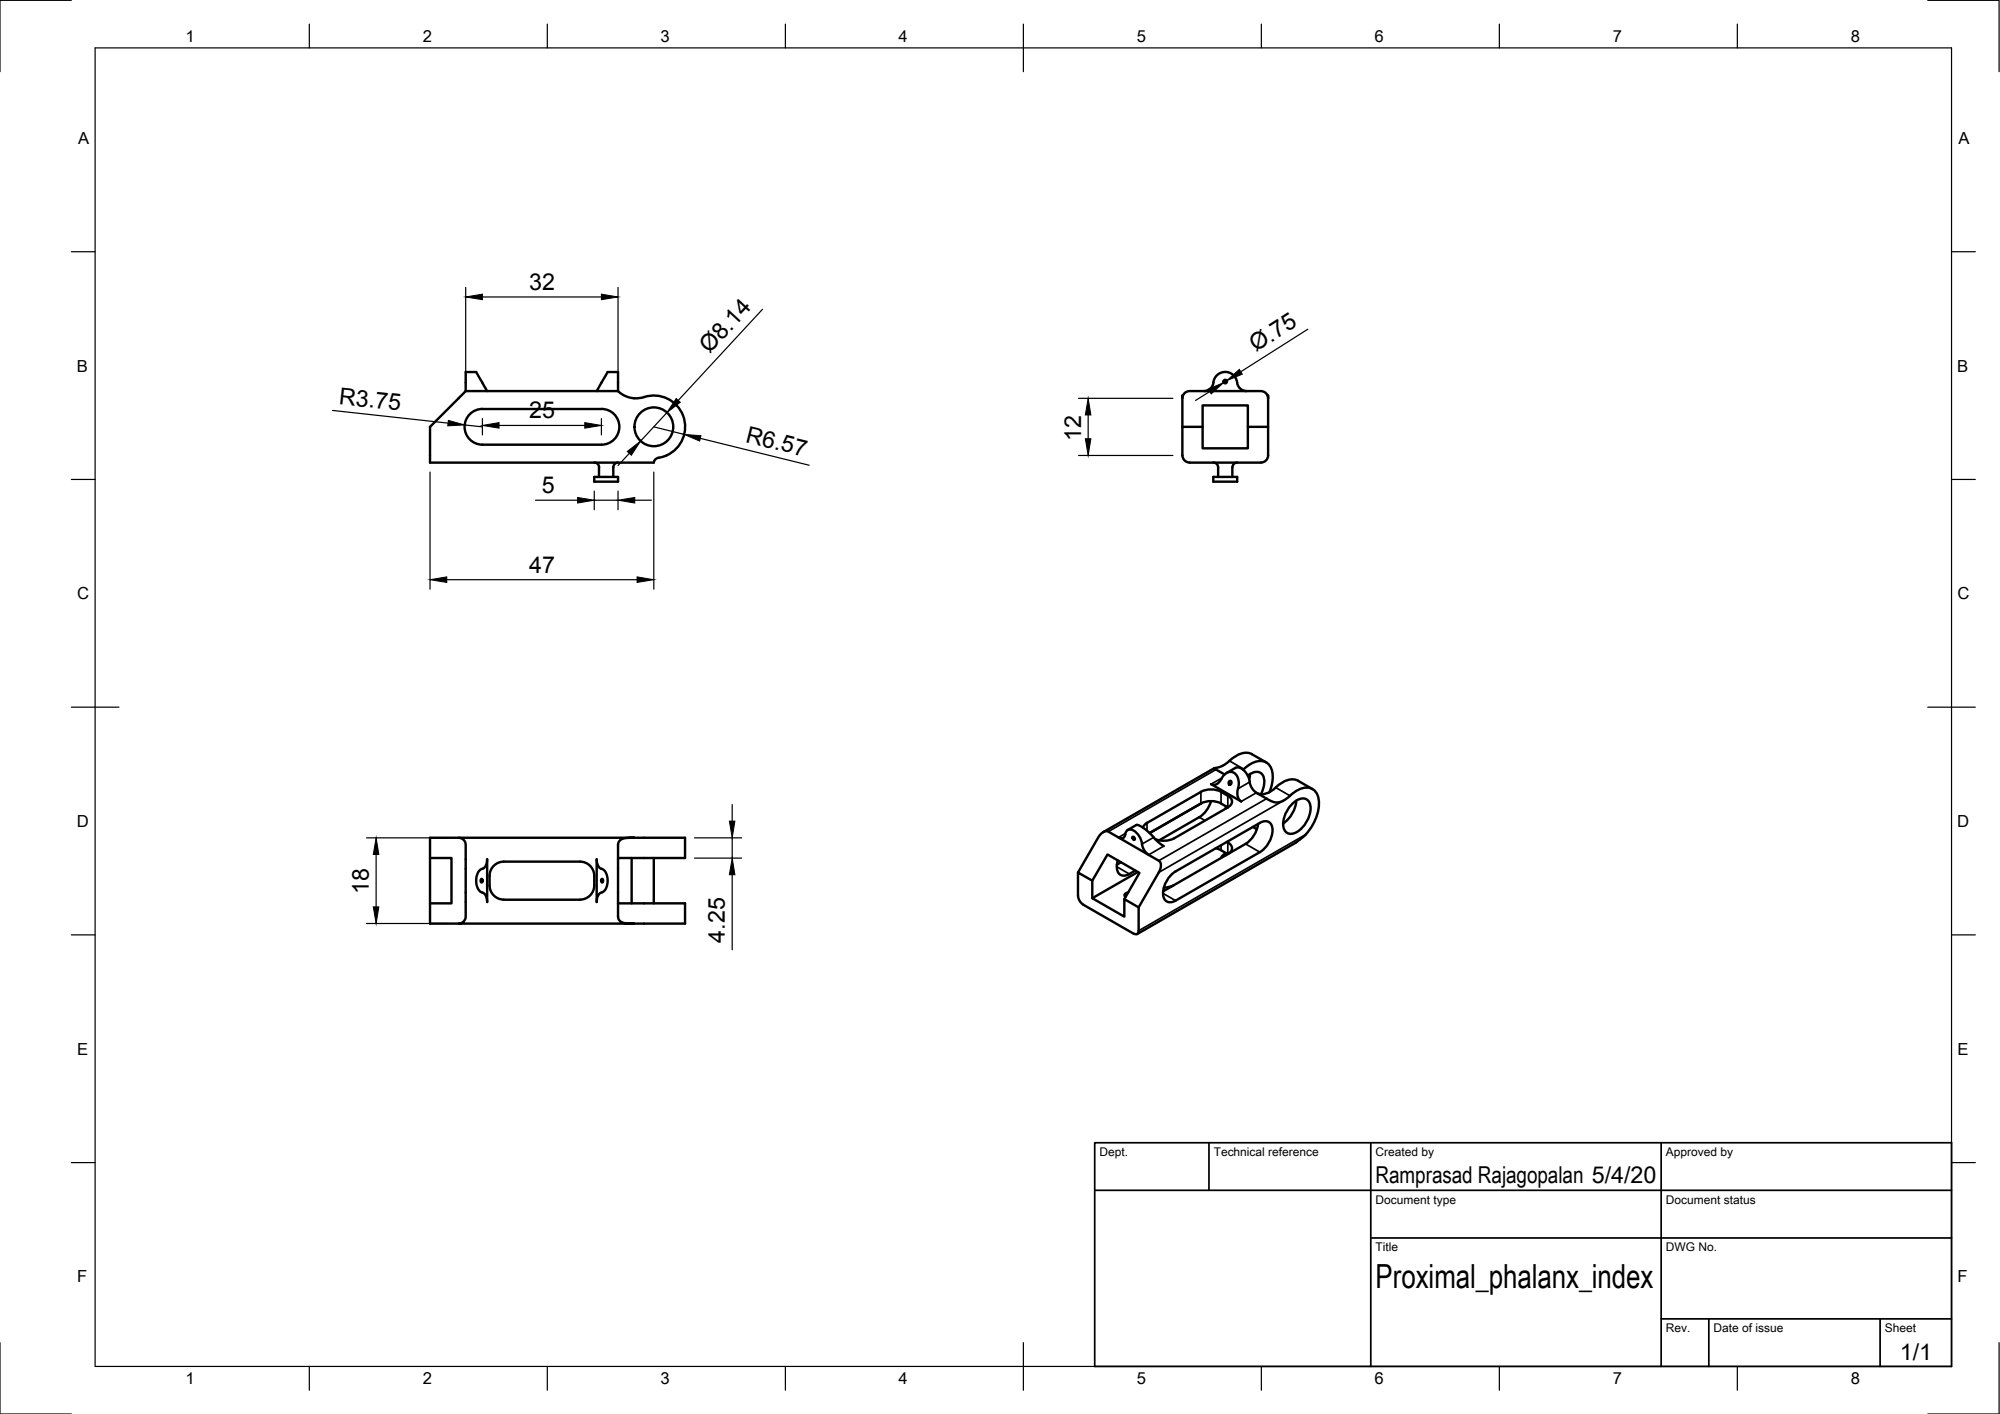
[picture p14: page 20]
Dept.; Technical reference; Created by; Approved by; Document type; Document status; Title; DWG No.; Proximal_phalanx_index; Ramprasad Rajagopalan

39

9.5 4.5

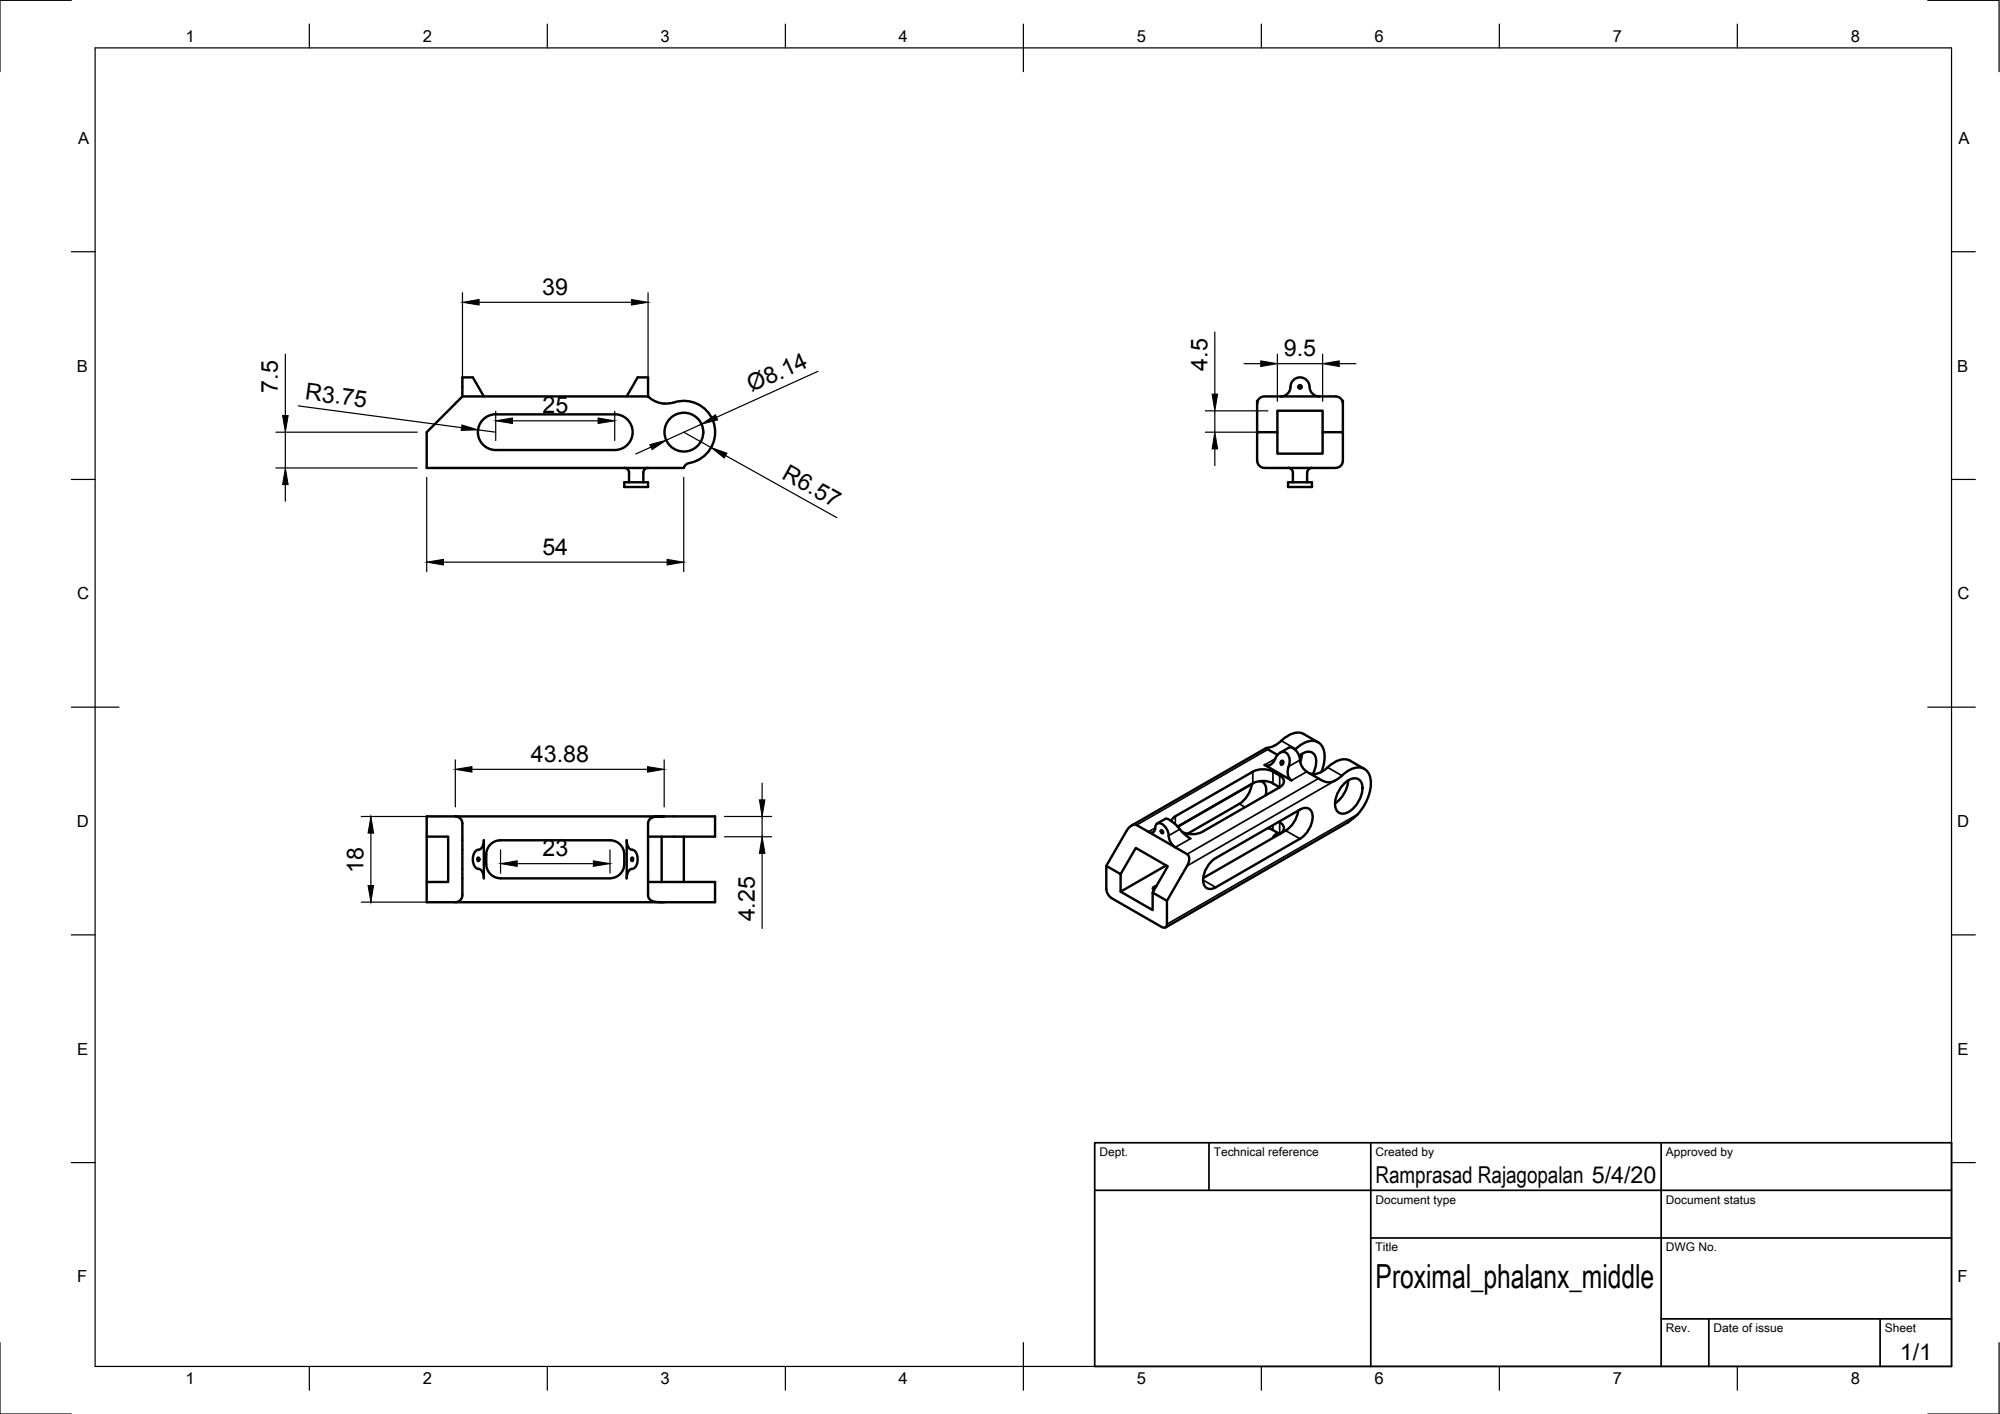
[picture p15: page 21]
Dept.; Technical reference; Created by; Approved by; Document type; Document status; Title; DWG No.; Proximal_phalanx_middle; Ramprasad Rajagopalan

20
9.5 4.5

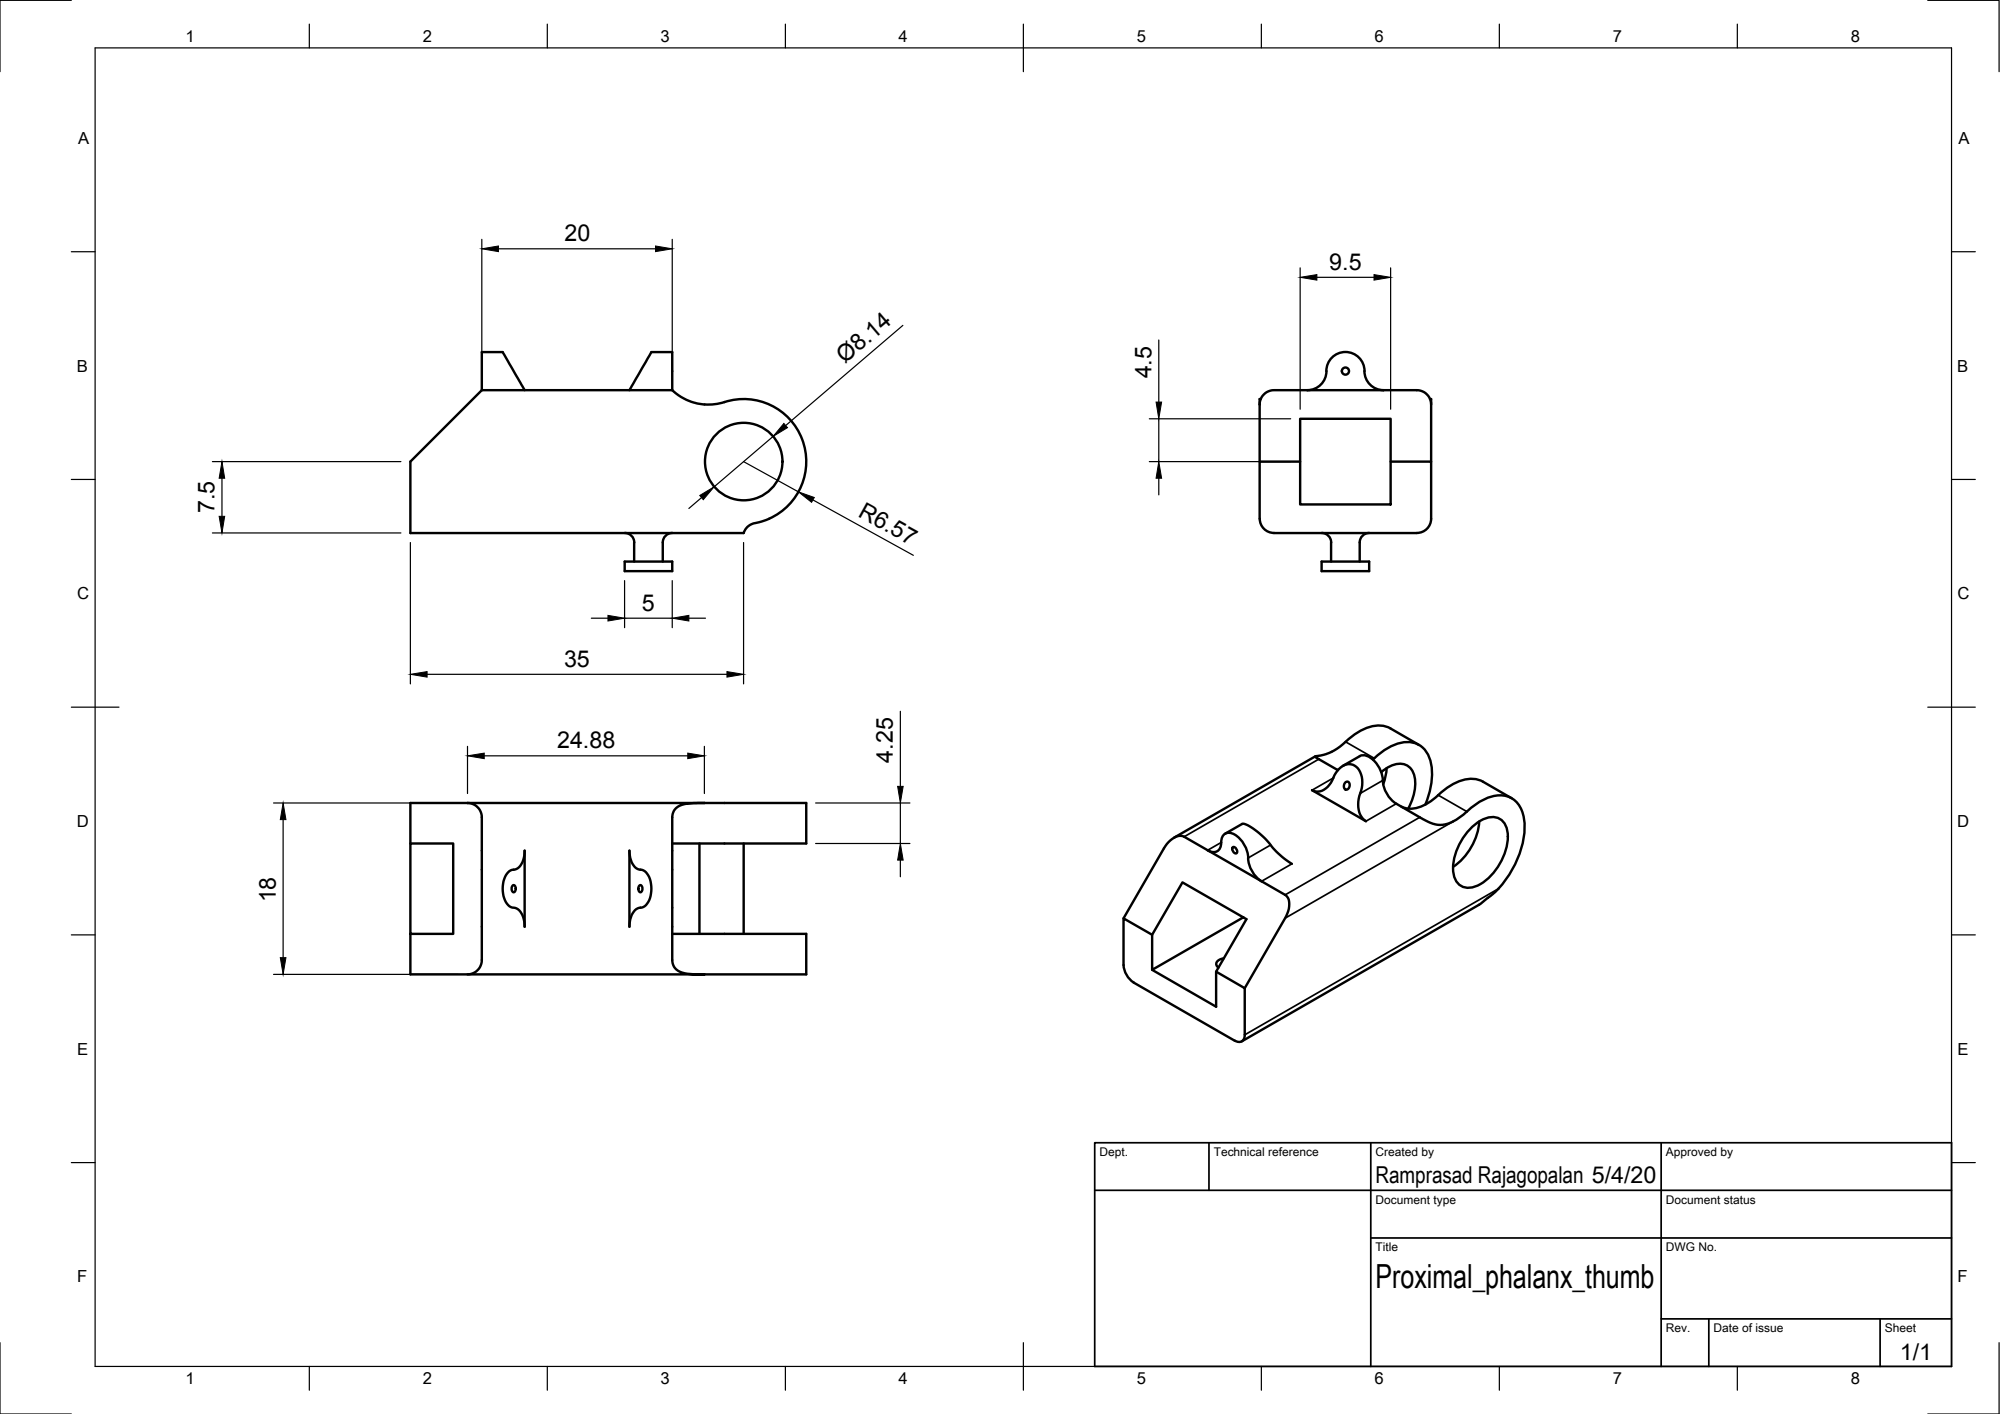
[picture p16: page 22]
Dept.; Technical reference; Created by; Approved by; Document type; Document status; Title; DWG No.; Proximal_phalanx_thumb; Ramprasad Rajagopalan

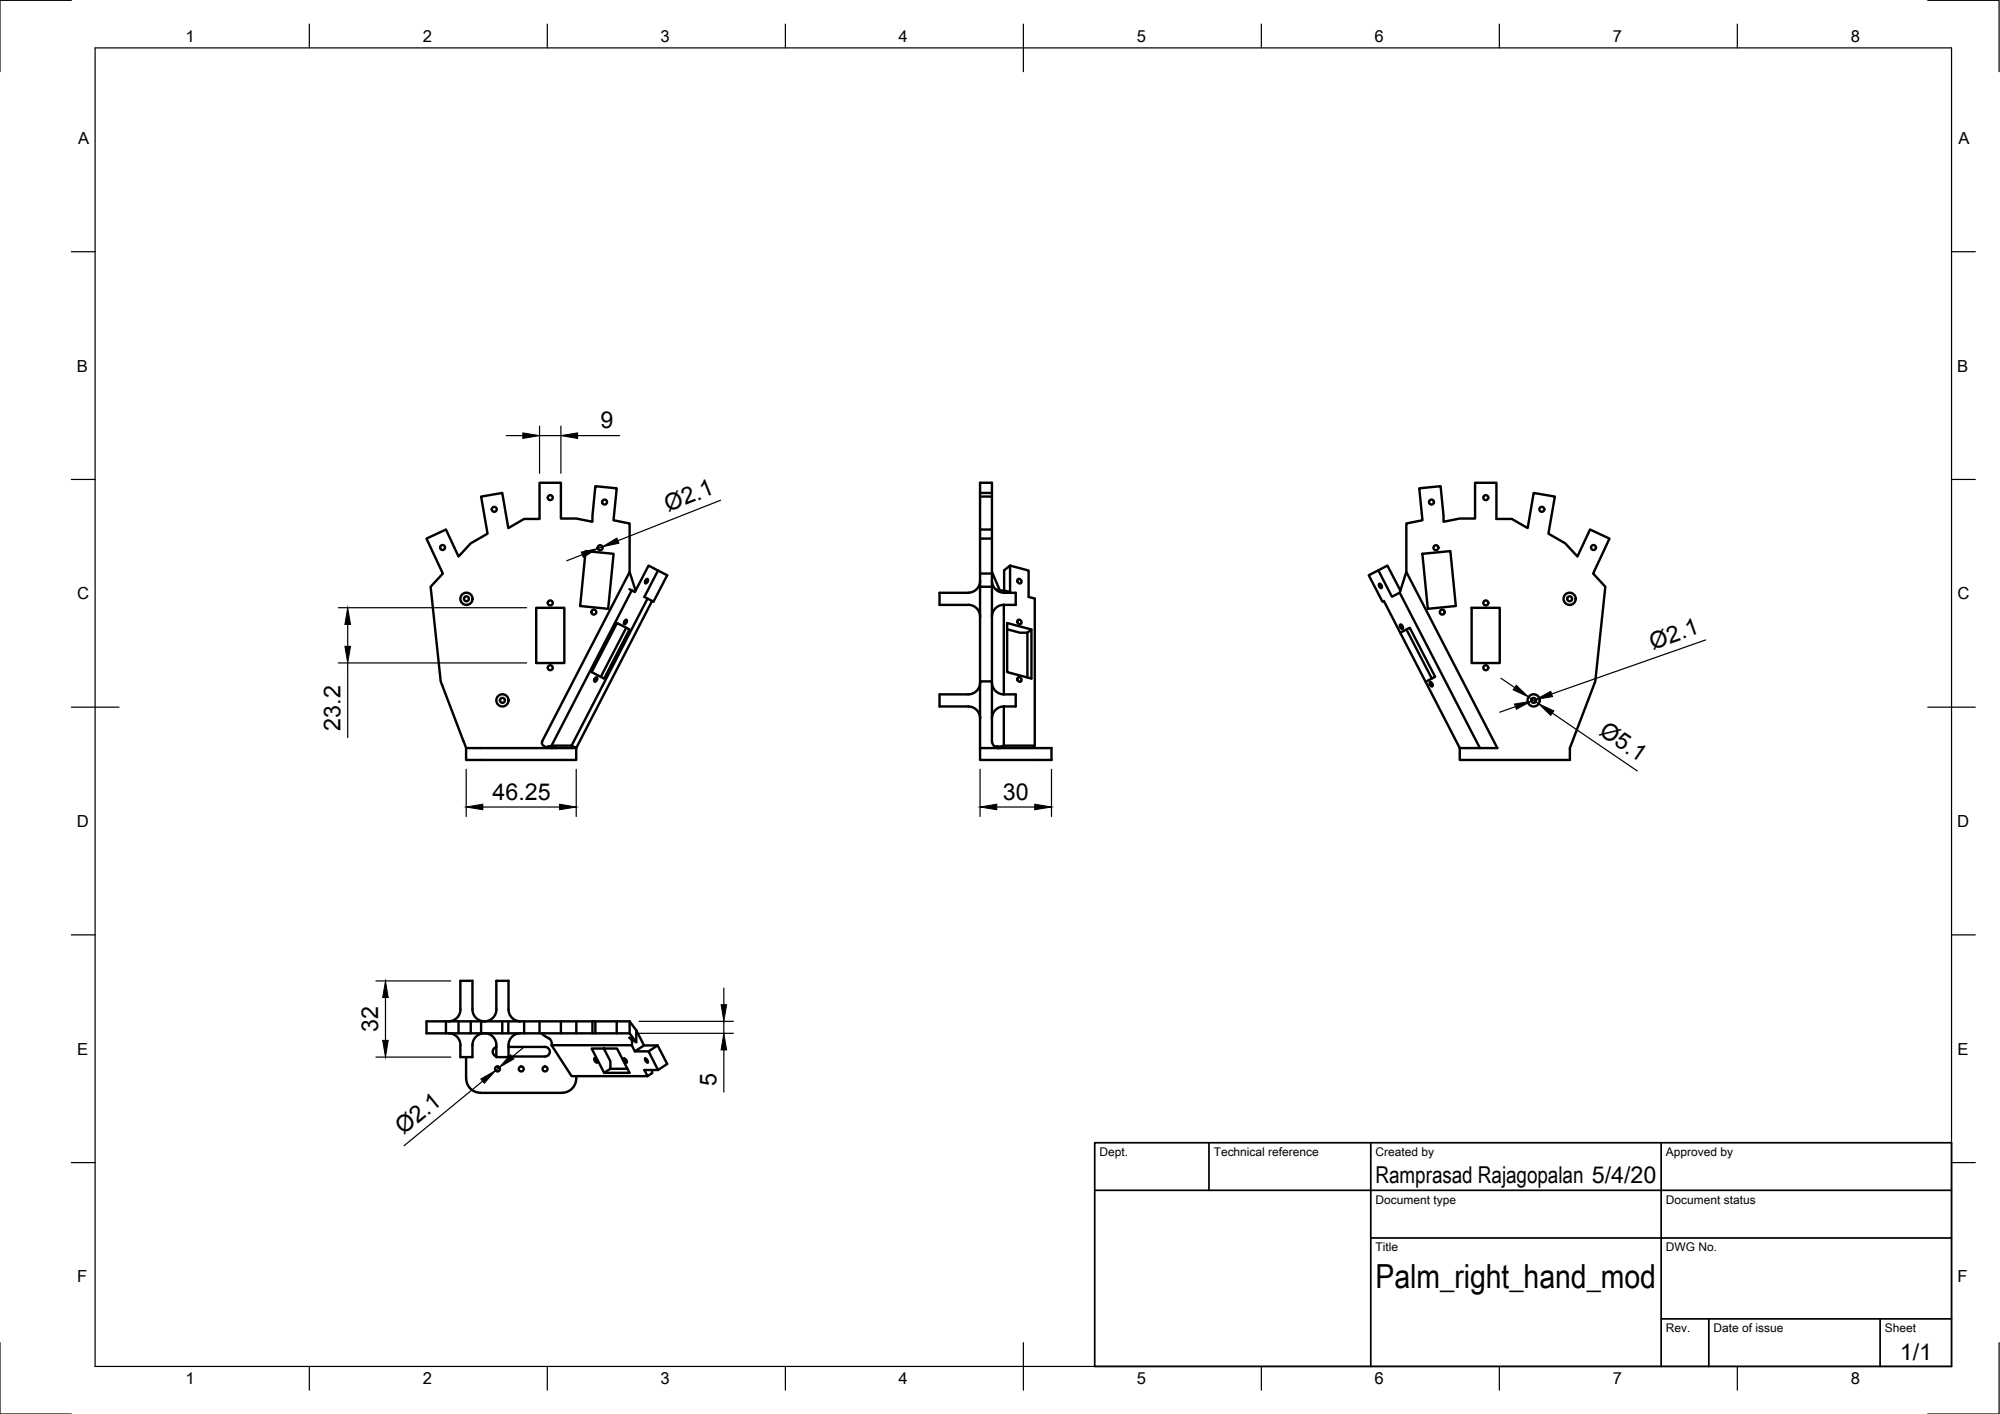
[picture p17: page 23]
Dept.; Technical reference; Created by; Approved by; Document type; Document status; Title; DWG No.; Palm_right_hand_mod; Ramprasad Rajagopalan

## Distal phalanx middle finger

## Intermediate phalanx middle finger

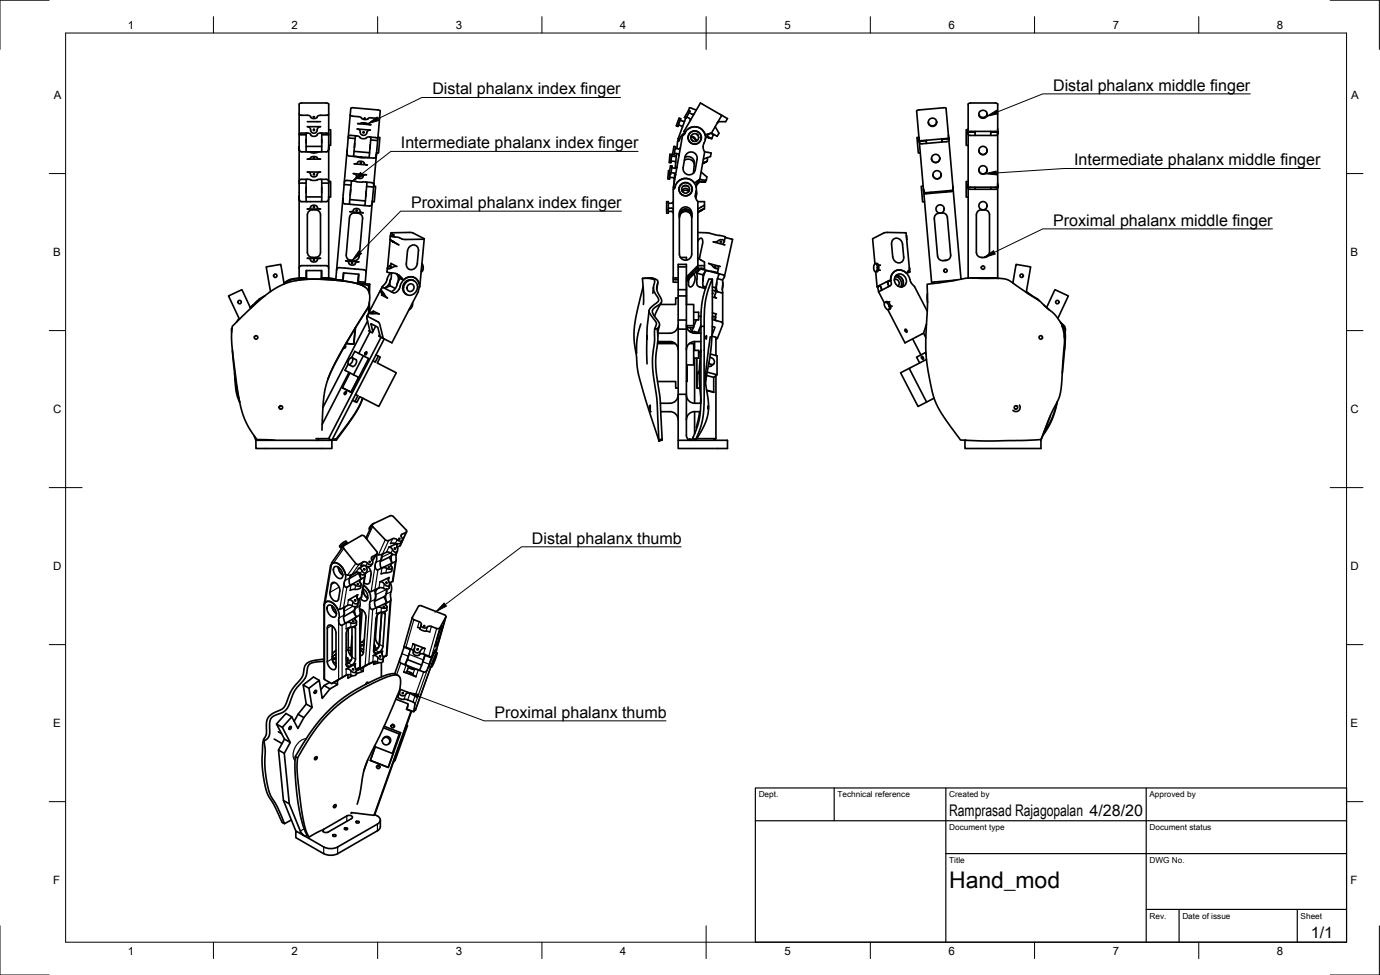
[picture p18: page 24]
Dept.; Technical reference; Created by; Approved by; Document type; Document status; Title; DWG No.; Hand_mod; Ramprasad Rajagopalan

Distal phalanx index finger

Intermediate phalanx index finger

Proximal phalanx index finger

Proximal phalanx middle finger

Distal phalanx thumb

Proximal phalanx thumb


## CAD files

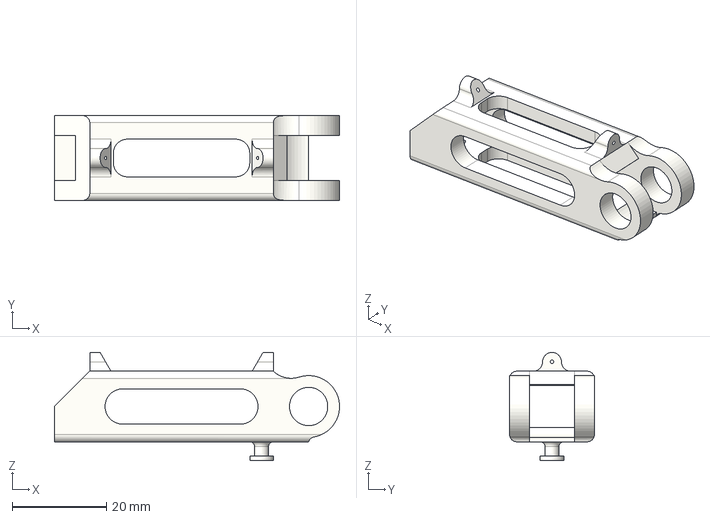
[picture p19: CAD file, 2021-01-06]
STEP_files/Proximal_phalanx_middle v5.step
60.6 x 18.0 x 23.0 mm

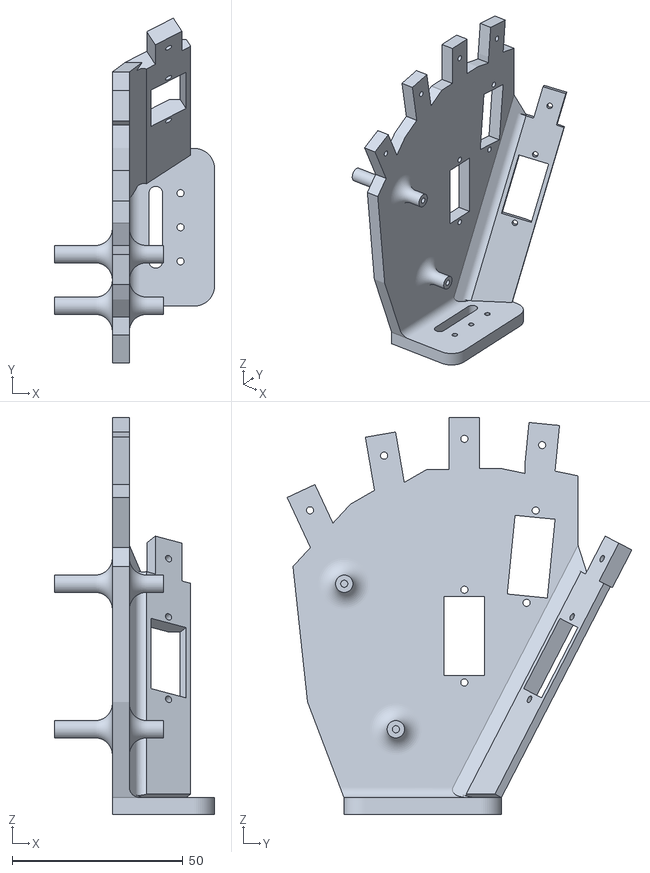
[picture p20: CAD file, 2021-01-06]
STLs/Palm_middle_part.stl
47.0 x 101.1 x 116.4

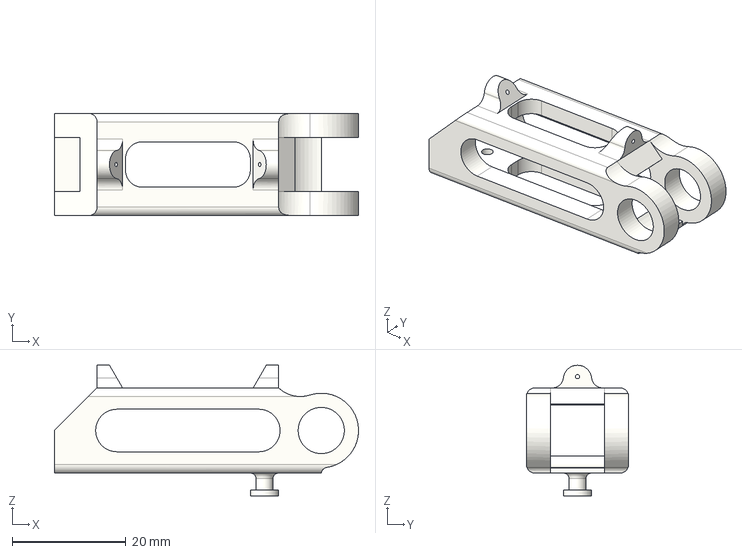
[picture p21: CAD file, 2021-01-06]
STEP_files/Proximal_phalanx_index v9.step
53.6 x 18.0 x 23.0 mm

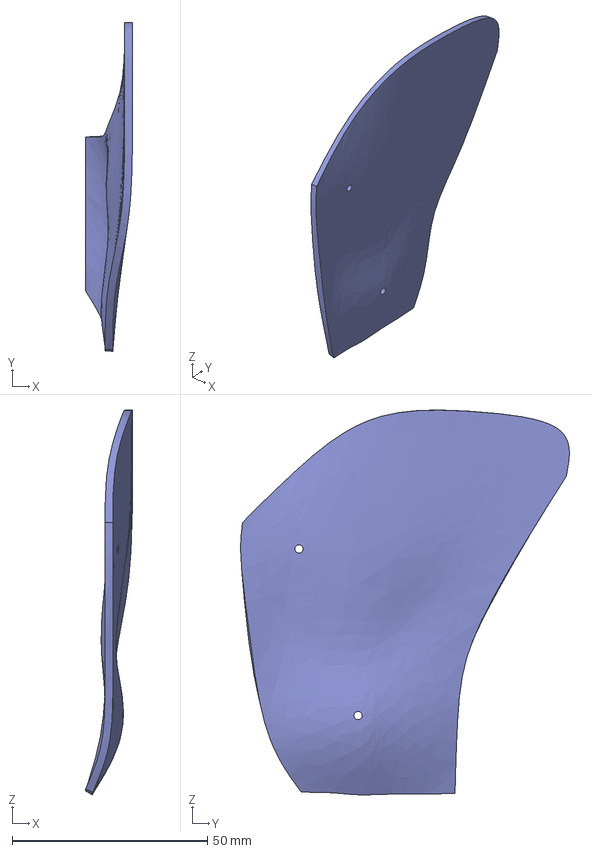
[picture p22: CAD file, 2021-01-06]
STEP_files/Palm_front v6.step
12.0 x 84.2 x 98.5 mm

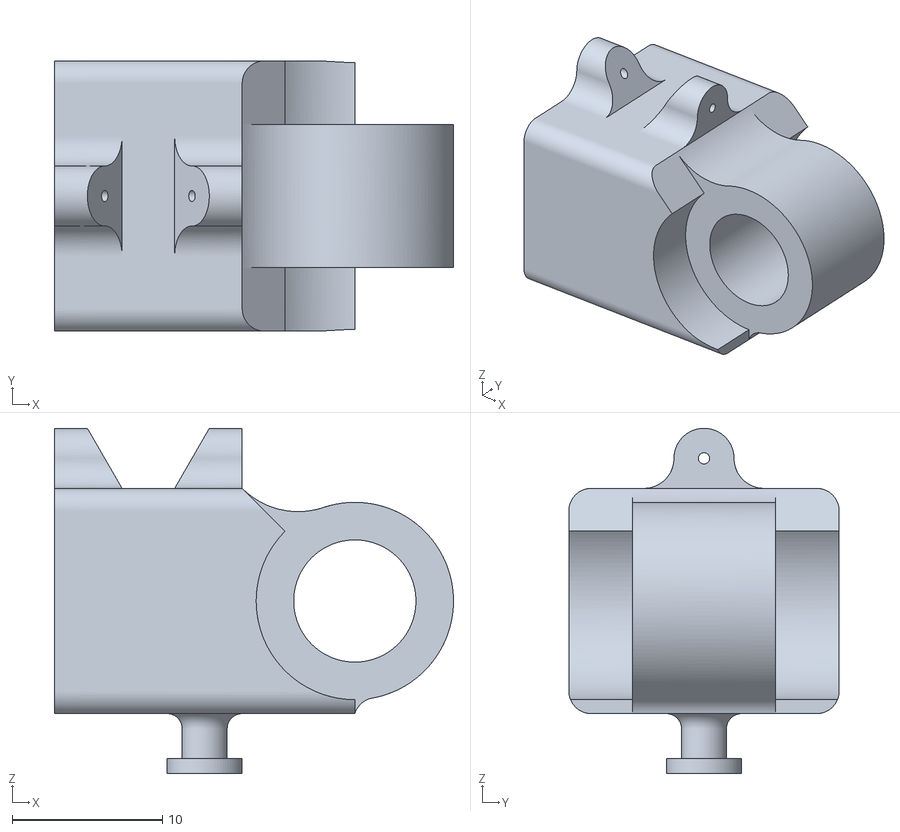
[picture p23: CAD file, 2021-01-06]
STLs/Distal_phalanx_middle.stl
26.6 x 18.0 x 23.0

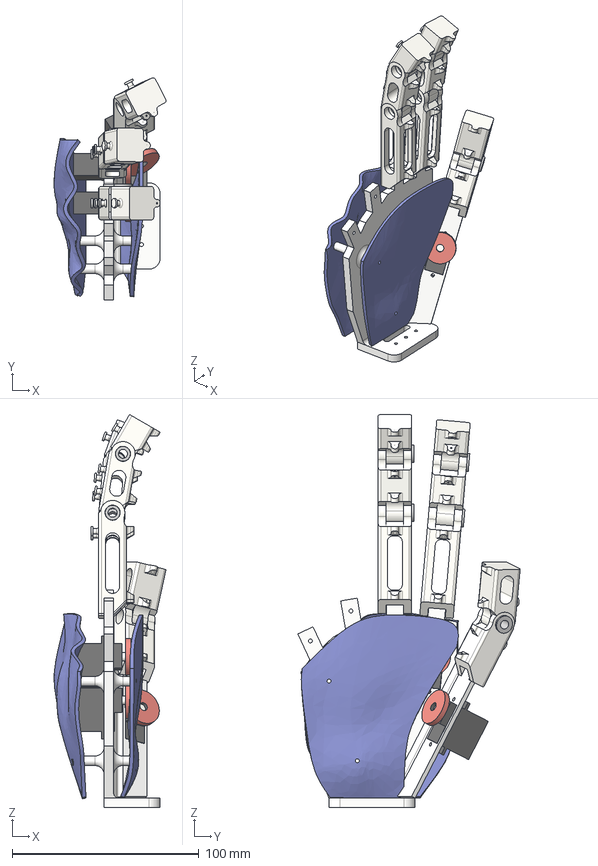
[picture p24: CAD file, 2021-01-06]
STEP_files/Hand_mod v8.step
60.0 x 119.1 x 210.5 mm
6294K433_LIGHT DUTY DRY-RUNNING SLEEVE BEARING x 5

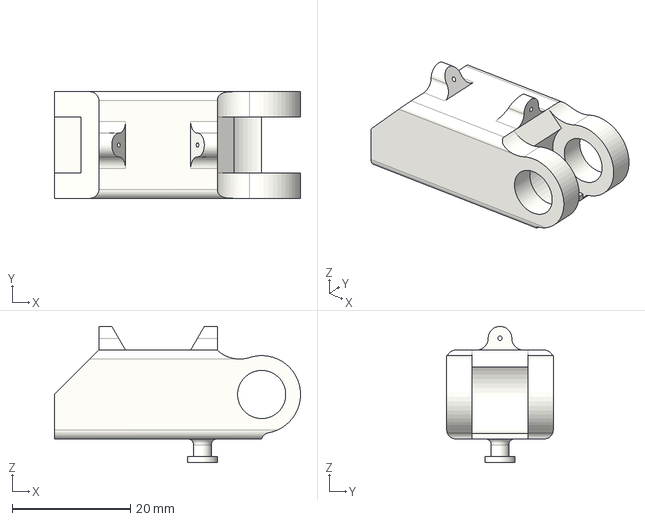
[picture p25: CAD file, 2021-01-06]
STEP_files/Proximal_phalanx_thumb v4.step
41.6 x 18.0 x 23.0 mm

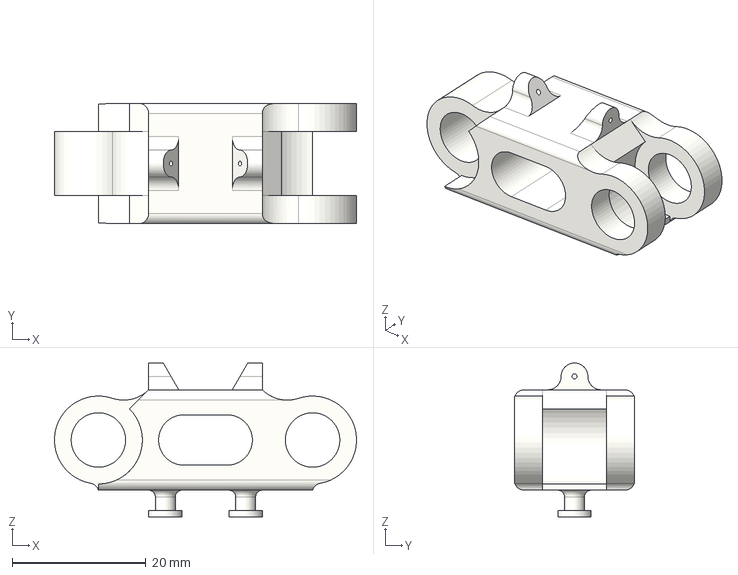
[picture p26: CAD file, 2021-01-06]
STEP_files/MIddle_phalanx_middle v4.step
45.1 x 18.0 x 23.0 mm

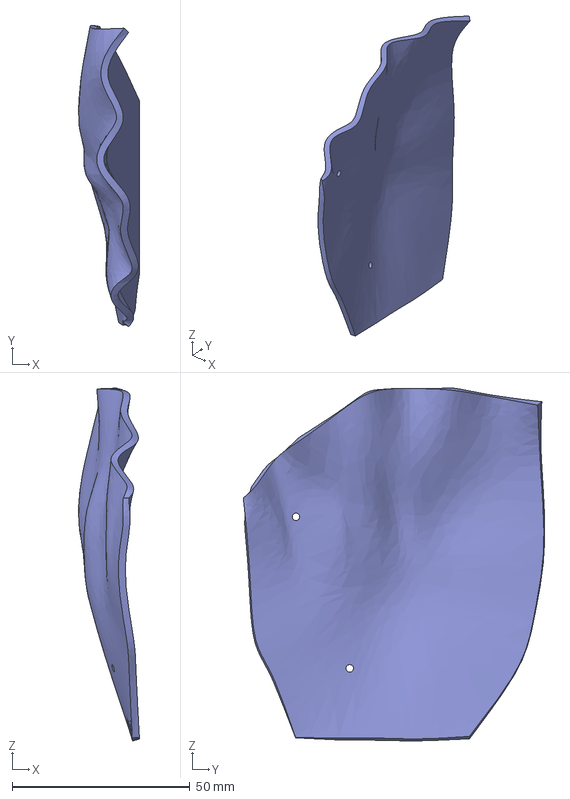
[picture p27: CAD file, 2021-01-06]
STEP_files/Palm_back v1.step
17.1 x 84.9 x 99.4 mm

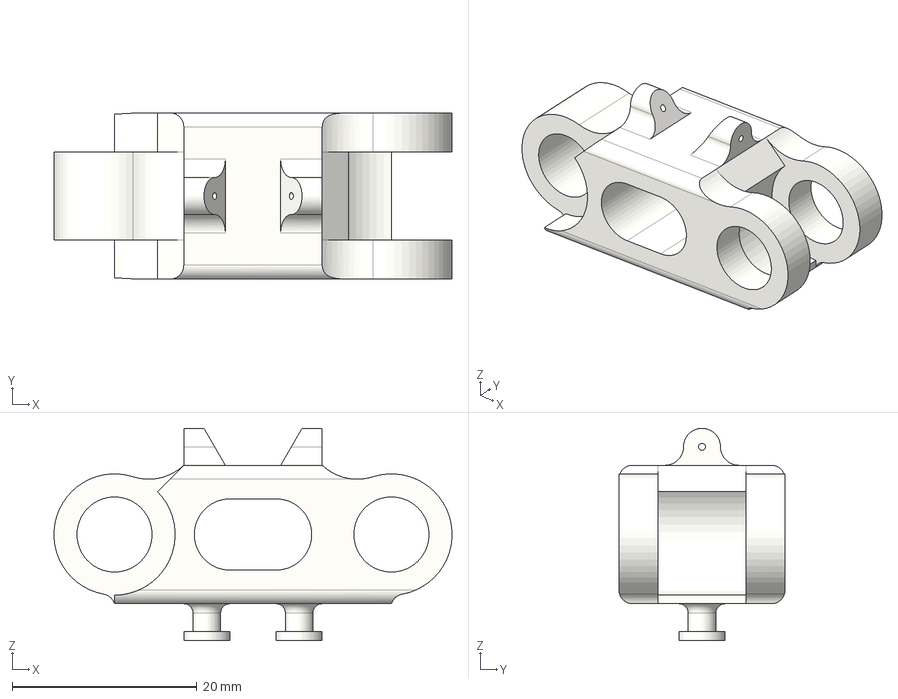
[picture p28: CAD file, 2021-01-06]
STEP_files/Middle_phalanx_index v5.step
43.1 x 18.0 x 23.0 mm

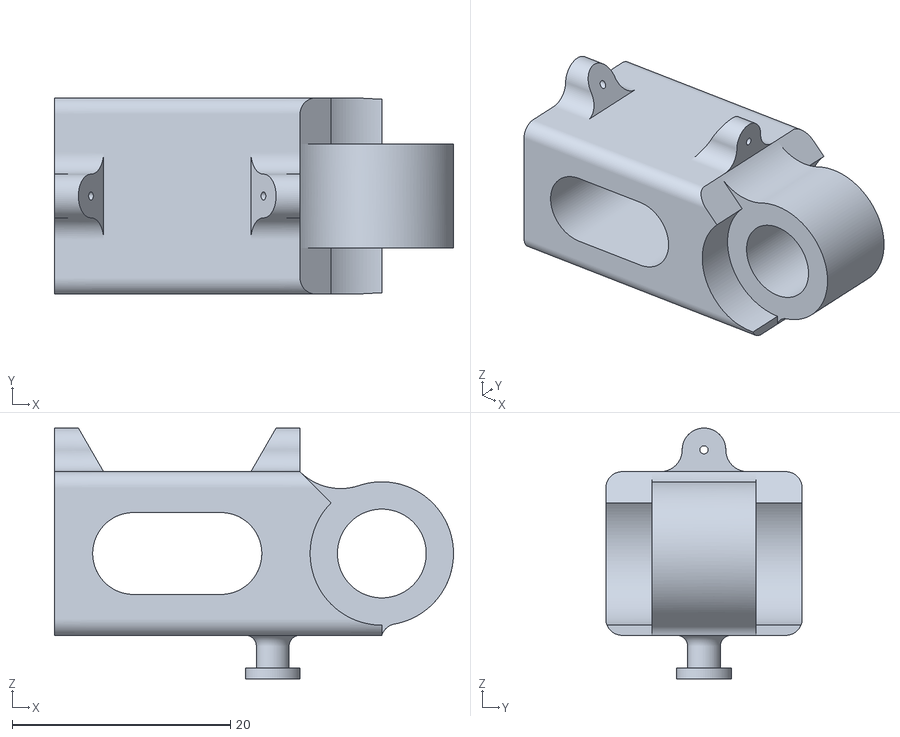
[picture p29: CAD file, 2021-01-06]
STLs/Distal_phalanx_thumb.stl
36.6 x 18.0 x 23.0

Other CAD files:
STLs/Proximal_phalanx_middle.stl
STLs/Distal_phalanx_index.stl
STLs/Proximal_phalanx_index.stl
STLs/Proximal_phalanx_thumb.stl
STLs/Middle_phalanx_middle.stl
STEP_files/Distal_phalanx_thumb v2.step
STLs/Middle_phalanx_index.stl
STEP_files/6294K433_LIGHT DUTY DRY-RUNNING SLEEVE BEARING v1.step
STEP_files/Distal_phalanx_index v4.step
STEP_files/Distal_phalanx_middle v2.step
STEP_files/Micro_servo v3.step
STEP_files/Palm_right_hand_mod v6.step

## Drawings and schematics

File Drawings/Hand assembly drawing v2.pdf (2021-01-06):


Distal phalanx index finger

Distal phalanx middle finger

Intermediate phalanx index finger

Intermediate phalanx middle finger

Proximal phalanx index finger

Proximal phalanx middle finger

Distal phalanx thumb

Proximal phalanx thumb

Dept. | Technical reference | Created by Ramprasad Rajagopalan 4/28/20 | Approved by

Document type | Document status

Title Hand_mod | DWG No.

Rev. | Date of issue | Sheet 1/1

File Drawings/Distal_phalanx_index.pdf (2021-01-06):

Ramprasad Rajagopalan 12

Dept. | Technical reference | Created by 5/4/20 | Approved by

Document type | Document status

Title Distal_phalanx_index | DWG No.

Rev. | Date of issue | Sheet 1/1

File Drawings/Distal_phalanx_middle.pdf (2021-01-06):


Dept. | Technical reference | Created by Ramprasad Rajagopalan 5/4/20 | Approved by

Document type | Document status

Title Distal_phalanx_middle | DWG No.

Rev. | Date of issue | Sheet 1/1

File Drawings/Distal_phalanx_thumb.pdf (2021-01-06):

Ramprasad Rajagopalan 12

Dept. | Technical reference | Created by 5/4/20 | Approved by

Document type | Document status

Title Distal_phalanx_thumb | DWG No.

Rev. | Date of issue | Sheet 1/1

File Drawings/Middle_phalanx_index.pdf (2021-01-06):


Dept. | Technical reference | Created by Ramprasad Rajagopalan 5/4/20 | Approved by

Document type | Document status

Title Middle_phalanx_index | DWG No.

Rev. | Date of issue | Sheet 1/1

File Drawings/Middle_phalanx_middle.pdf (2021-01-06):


Dept. | Technical reference | Created by Ramprasad Rajagopalan 5/4/20 | Approved by

Document type | Document status

Title MIddle_phalanx_middle | DWG No.

Rev. | Date of issue | Sheet 1/1

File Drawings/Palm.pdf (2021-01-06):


Dept. | Technical reference | Created by Ramprasad Rajagopalan 5/4/20 | Approved by

Document type | Document status

Title Palm_right_hand_mod | DWG No.

Rev. | Date of issue | Sheet 1/1

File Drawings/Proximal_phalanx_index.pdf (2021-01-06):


Dept. | Technical reference | Created by Ramprasad Rajagopalan 5/4/20 | Approved by

Document type | Document status

Title Proximal_phalanx_index | DWG No.

Rev. | Date of issue | Sheet 1/1

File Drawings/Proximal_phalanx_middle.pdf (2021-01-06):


Dept. | Technical reference | Created by Ramprasad Rajagopalan 5/4/20 | Approved by

Document type | Document status

Title Proximal_phalanx_middle | DWG No.

Rev. | Date of issue | Sheet 1/1

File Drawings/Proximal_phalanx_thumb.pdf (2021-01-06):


Dept. | Technical reference | Created by Ramprasad Rajagopalan 5/4/20 | Approved by

Document type | Document status

Title Proximal_phalanx_thumb | DWG No.

Rev. | Date of issue | Sheet 1/1

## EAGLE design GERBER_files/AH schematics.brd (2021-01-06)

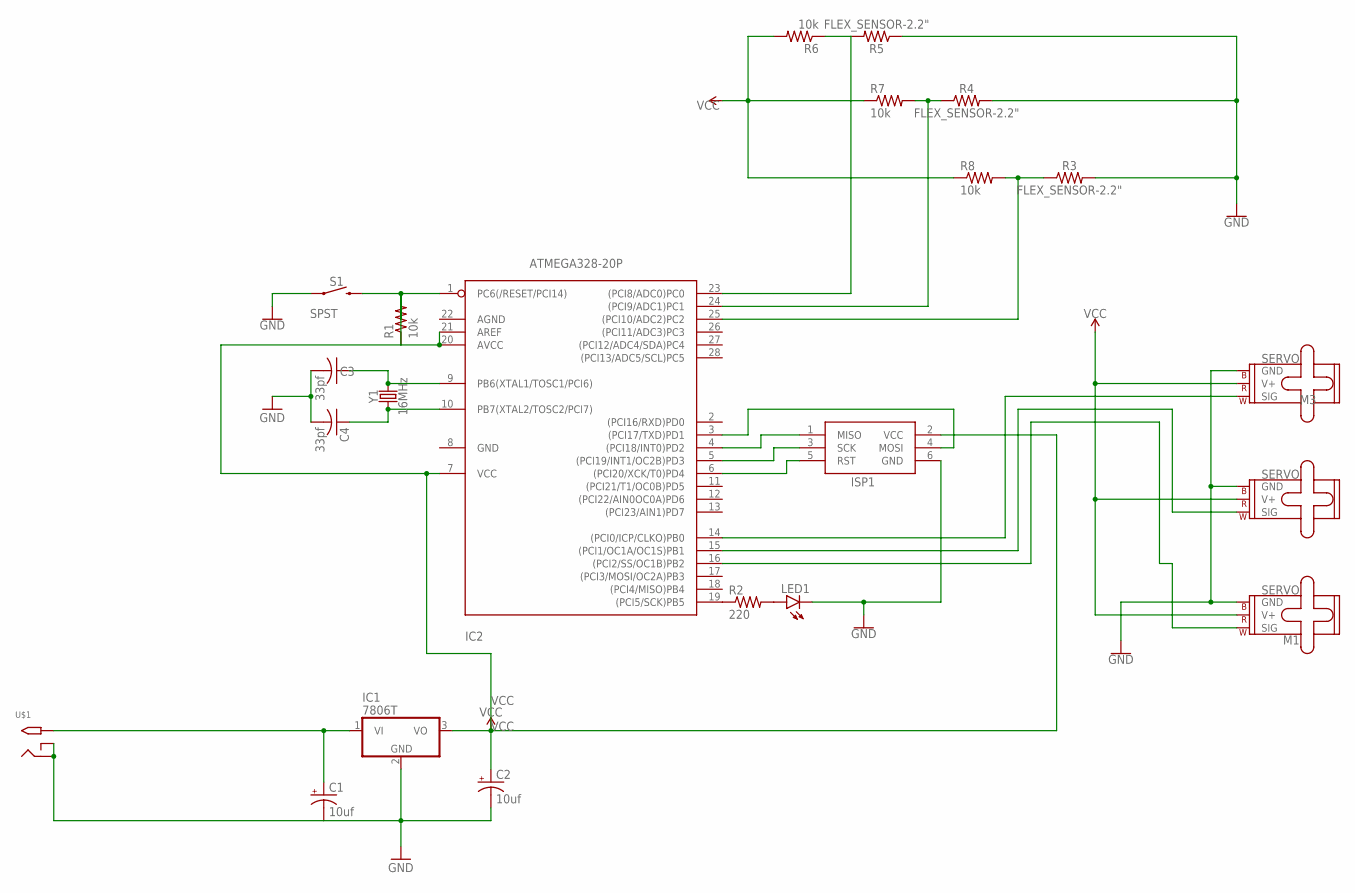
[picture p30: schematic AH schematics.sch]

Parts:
C1, C2: 10uf; E3,5-8
C3, C4: 33pf; C025-024X044
IC1: 7806T; TO220H
IC2: ATMEGA328-20P; DIL28-3
ISP1: AVRISP-6; AVRISP
LED1: LED3MM
M1, M2, M3: SERVO; 1X03
R1, R6, R7, R8: 10k; 0204/7
R2: 220; 0204/7
R3, R4, R5: FLEX_SENSOR-2.2"; FLEX_SENSOR
S1: SPST; TACTILE_SWITCH_PTH_6.0MM
U$1: 2.1MMJACKSMT; DCJACK_2MM_SMT
Y1: 16MHz; HC49US

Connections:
GND: C1.-, C2.-, C3.2, C4.2, IC1.2 (GND), ISP1.6 (GND), LED1.A, LED1.K (C), M1.3 (GND), M2.3 (GND), M3.3 (GND), R2.2, R3.P$2 (2), R4.P$2 (2), R5.P$1 (1), S1.1, U$1.GND (RING), U$1.GNDBREAK (RING_SW)
unnamed: C1.+, IC1.1 (VI), U$1.PWR2 (TIP)
unnamed: IC2.19 ((PCI5/SCK)PB5), R2.1
unnamed: IC2.1 (PC6(/RESET/PCI14)), R1.1, R1.2, S1.3 (2)
unnamed: C3.1, IC2.9 (PB6(XTAL1/TOSC1/PCI6)), Y1.2
unnamed: C4.1, IC2.10 (PB7(XTAL2/TOSC2/PCI7)), Y1.1
unnamed: IC2.16 ((PCI2/SS/OC1B)PB2), M1.1 (SIG)
unnamed: IC2.14 ((PCI0/ICP/CLKO)PB0), M3.1 (SIG)
unnamed: IC2.5 ((PCI19/INT1/OC2B)PD3), ISP1.3 (SCK)
unnamed: IC2.6 ((PCI20/XCK/T0)PD4), ISP1.5 (RST)
unnamed: IC2.4 ((PCI18/INT0)PD2), ISP1.1 (MISO)
unnamed: IC2.3 ((PCI17/TXD)PD1), ISP1.4 (MOSI)
unnamed: IC2.24 ((PCI9/ADC1)PC1), R4.P$1 (1), R7.2
unnamed: IC2.23 ((PCI8/ADC0)PC0), R5.P$2 (2), R6.1
unnamed: IC2.25 ((PCI10/ADC2)PC2), R3.P$1 (1), R8.2
unnamed: IC2.15 ((PCI1/OC1A/OC1S)PB1), M2.1 (SIG)
VCC: C2.+, IC1.3 (VO), IC2.7 (VCC), IC2.20 (AVCC), IC2.21 (AREF), ISP1.2 (VCC), M1.2 (V+), M2.2 (V+), M3.2 (V+), R6.2, R7.1, R8.1

Board: 2 copper layers, 22 parts (0 on the bottom side), 17 nets, no tracks yet.

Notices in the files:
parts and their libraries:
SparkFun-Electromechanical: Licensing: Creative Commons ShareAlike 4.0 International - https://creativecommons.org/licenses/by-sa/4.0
